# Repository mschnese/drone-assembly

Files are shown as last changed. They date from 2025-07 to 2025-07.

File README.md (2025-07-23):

# drone-assembly

## Objective: Build a drone from start to finish. I wanted to treat this like a rigorous personal project. I established a timeline, a budget, optimized my BOM, 3d modeled and printed my drone's frame, analyzed the frame through FEA and tests in real life, made every decision based on a justification, documented every step, and created a writeup for it.

## Contents: Assorted media from each stage of the project and the technical report

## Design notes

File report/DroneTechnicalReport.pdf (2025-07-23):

Matthew Schnese | 1

# Independent Drone Project

Building a Drone Utilizing CAD, FEA, Iterative Prototyping, and Betaflight Tuning.

## Matthew Schnese

6/23/2025

## Abstract:

The goal of this project was to build a functional quad copter drone capable of stable flight leveraging an engineering skillset, all while treating the project as a rigorous engineering endeavor. This included a bill of materials, a timeline, designing the drone’s frame, and justification for each action taken. Overall, the project encountered hurdles from every step. Some were entirely user errors, like poor solders, and others were inevitable, such as software issues. Some errors, however, were due to inexperience in engineering projects, such as GD&T or weight and size considerations. These errors were extremely valuable to learn from firsthand. The result of the project was a successful controlled flight; however, a critical failure of an ESC has grounded the project for the time being. While this is unfortunate, this is not a stopping point for this project but rather a simple part replacement.

## Table of Contents:

### 1. Introduction: pg. 4

### 2. Methodology: pg. 5

### 3. Analysis and Results: pgs. 6-8

### 4. Challenges and Conclusion: pg. 9

### 5. References: pg. 10

### 6. Appendices: pg. 11-14

## Introduction:

This report documents the design and construction of a drone, which was built as a

personal project during the summer break in between semesters. The motivations of this project

were to tackle an engineering project without guidance and to satisfy personal curiosity. This

project was meant not to be an informal side project, but rather a strict, well documented, and

rigorous project that would better mimic real life. A scope was established with the conception of

this project, and every design decision was documented thoroughly. Along with this, there was

also a tangible goal for success for each step of the drone assembly.

The scope of this project, from the start, has been well defined; the final drone design was

intended to be handheld, and flown via line of sight. Additionally, the weight of the drone was

monitored to comply with FAA regulation. Drones that weigh more than 250g must be registered

with the FAA [1], so keeping the drone under 250g was essential. For the design of the drone, I

decided to model the drone’s frame using SolidWorks, but elected not to build the flight

controller manually to avoid scope creep. Additionally, a timeline was decided after initial

research as part of the scope, which was a total of 6 weeks from start to finish. The timeline for

this project was as follows: week 1 was research, week 2 was computer assisted design (CAD)

modeling, week 3 was frame testing and software familiarization, week 4 was assembly, week 5

was flight testing, and week 6 was reserved for delays and final touches. This was primarily to

avoid the feeling of a side project, but rather to make this an active project that required near

constant work, which better mimics an actual engineering project.

## Methodology:

At the beginning of this project, the parts were researched and chosen based on the clear

scope that had been developed. These parts were then compiled into a complete Bill of Materials,

which can be seen in appendix D. For this design project, a 4000kv brushless motor and the

propellers built for it were chosen due to the motor’s relatively low power, matching the scope of

the handheld drone. A 3S 850mAh LiPo battery was also chosen to complement the motor. The

selected flight controller was the Speedy Bee 405AIO, which has many DIY friendly features

like integrated electronic speed controllers (ESCs), BetaFlight software support, and a compact

size that serves well for smaller builds. Over the course of the project 3 prototypes were created.

The frame of the drone was a completely original work created with a combination of

CAD and additive manufacturing, specifically 3D printing. The drone’s frame was split into three

parts, the main body, the body’s lid, and modular arms. The main body was designed in a basket

shape with a size of 70mm×70mm×25mm, but later iterations increased the size to 85×85×30,

which let components fit better. The arms are 50mm long overall, featuring a hollowed-out well

for the motors to be mounted and 2 screws to mount the arm to the main body. This decision

allows for broken arms to be isolated and requires only a single arm to be made, not the entire

frame. The entire design was optimized for easy assembly, requiring 12 m3x8mm screws, with 4

for the lid and 2 for each arm.

For the 3D printing of the frame, specific choices were made to maximize the strength of

the drone’s frame while minimizing weight. All three parts of the frame were printed using

PLA+, which was chosen due to material availability at the time. Additionally, the frame was

printed with a 30% infill, which means the printed part has 30% of the normal density of the

printing material, and a gyroid pattern which is a great choice for strength in all directions.

Supports were used, but only on overhangs that were over the build plate. This design decision

stopped supports from printing in hard-to-reach places, which was easier for assembly but

slightly reduced strength because of inefficient first layer bonding on some overhangs. Some

other minor print settings included a nozzle temperature of 215° C and a build plate temperature

of 65° C. Once the frame was printed, the edges were sanded, and the supports were removed.

## Analysis and Results:

The drone frame was analyzed using both finite element analysis (FEA) and real-life

testing. While FEA testing was only performed for the final design, each prototype was tested in

real life. The tests performed were a drop test at various heights, a load test for both the frame

and the arm, and weighing the drone to ensure flight was possible. The drop tests were conducted

on concrete, starting at one foot and increasing in increments of one foot each time until a height

of six feet. While the drone was not dropped with a simulated load weight, it is believed that the

rough concrete mitigated this potential source of error in testing. The load tests performed for the

main body and the arm were a load of 200lb and a load of 2lb respectively. These tests can be

seen in appendix A. The weight of the frame did not have a strict value in mind, but for flight to

be possible (and responsive), a weight of 50-100g was required for the full frame.

The first prototype passed all the load tests but could not be assembled because the

intended screw holes were not wide enough and screws were stripped during assembly. The first

prototype also failed the weight requirement with a weight of 46g, just under the lower limit. The

second prototype was able to be assembled, increased in size for better part accommodation, and

passed every test except the drop test, which had an arm break on the 6ft drop due to a force

concentration, all while weighing 96g. The third prototype increased the strength of the arm and

the connection while shaving weight and resulted in the same experimental outcome as the

second prototype while weighing 88g. It is worth noting that the severity of the break, while the

same in nature, decreased in severity from the second and third prototype. While these breaks do

showcase a failure point, breaking at the arm connection is preferred due to the modular nature

of the arm, and therefore is not a failure structurally. Since the electronics inside the main frame

are worth far more than the motor and arm, even if the motor is permanently damaged that is a

better outcome than the overall body receiving a large impact and breaking. Images of these

breaks can be seen below in Figure 1a and 1b.

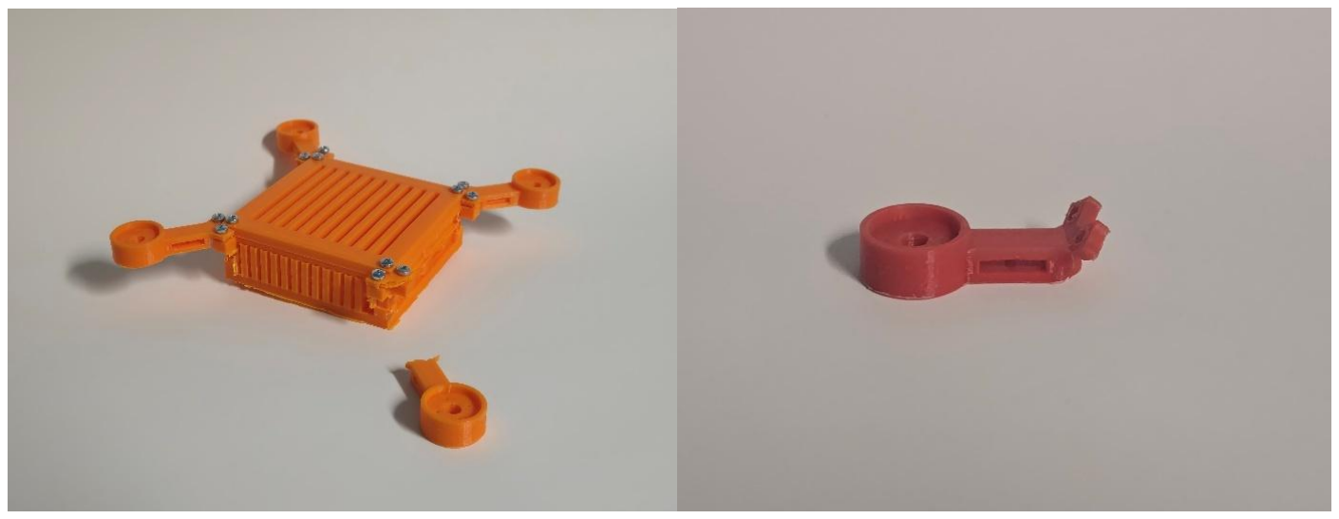
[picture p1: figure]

Figure 1: Drop Test Breaks – (a) Prototype 2, (b) Prototype 3

For the final design, FEA testing was implemented with five studies overall: two on the

arm and three on the body. For the arm, studies were run for lift forces and torque from the

motor, with the failure load and torque found to be 7.885 lbf and 15.76 lbf ·in respectively.

According to the manufacturer, the chosen motor’s maximum thrust on a 4S LiPo battery per

motor is 290g [2]. For a 3S battery setup like the one in this project, a maximum lift of about 200

g or 0.44 lbf is more practical, which is way below the failure point of the arm. The torque

generated by the motor was calculated using Equation 1, which can be seen below.

T = tℎrust × rpropeller

Since the propeller for this project has a 2.5-inch diameter, the total torque produced by

one motor is 0.55lbf ·in, which is well below the yield strength of the arm as well. While the arm

performed very well on the FEA analysis, it is worth pointing out that the failure point in FEA

also correlates with real life very well. This can be seen below in Figure 2.

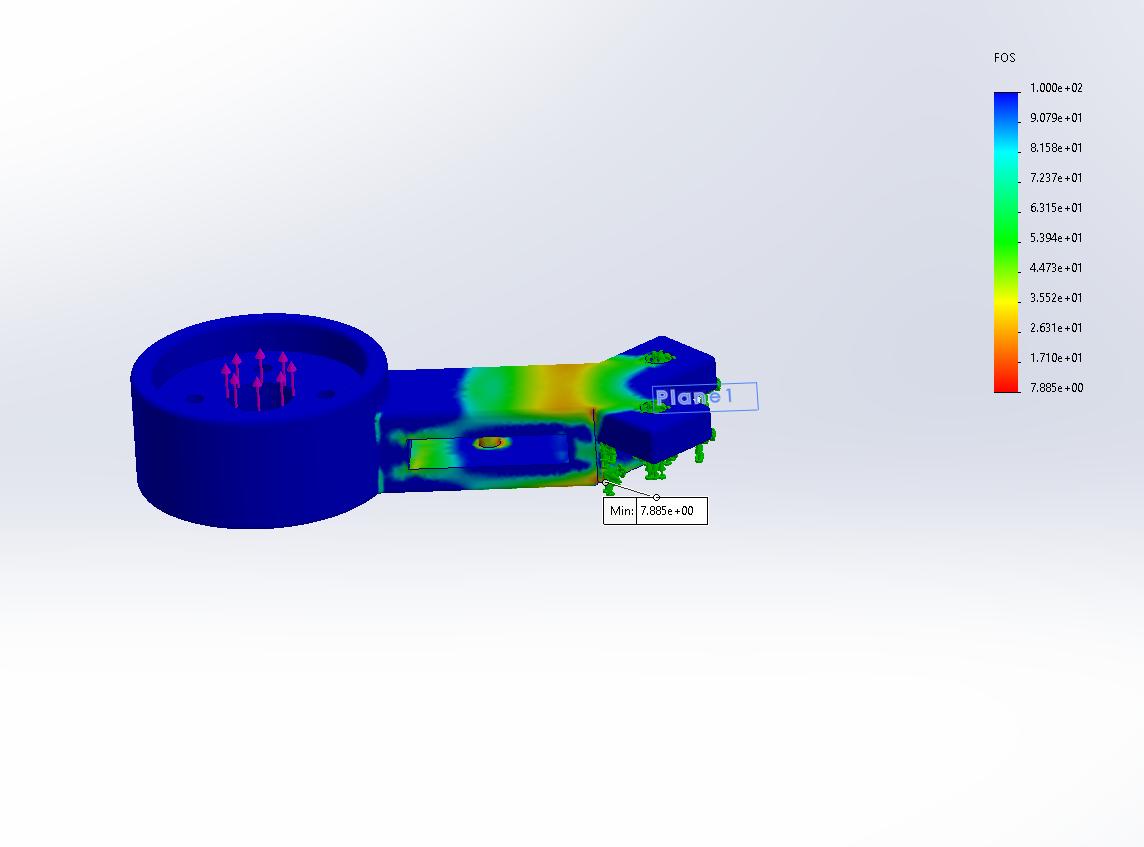
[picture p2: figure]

Figure 2: FEA Analysis Failure Points for Lift

For the body, similar studies were run concerning lift and torque on the connection where

the arm attaches, and a study was run on the load that the base of the drone frame could

withstand. For the lift and torque studies, the main connection point had a failure load and torque

of 122.3 lbf and 8.895 lbf·in respectively. For the load study, the analysis showed a maximum

load of 111.6 lbf. This particular result was interesting since real load testing showed that the

frame survived loads of 200 lbf. Because of this discrepancy, further load testing was conducted,

and it was found that the drone body could withstand over 285 lbf of load without breaking. This

highlights the differences between FEA analysis and real testing.

## Challenges and Conclusion:

During this project, there were many engineering challenges that had to be overcome.

From frame design to thermal issues on the flight controller, every step had a major issue that

needed to be addressed. During the initial frame design, many issues were discovered after

manufacturing the frame. From the size of the frame to the size of the screw holes to the design

of the arms, each piece was fine in theory but turned out to not work practically due to things like

GD&T. Soldering was also a major hurdle, since I have little soldering experience. The wiring

diagram for this project can be seen in appendix B. The connection wires for the battery and the

wires to the motors were a large gauge, which was a challenge to solder properly with the small

flight controller pads. Additionally, since this system underwent crashes during flight tests and

the wires were bent to accommodate space, often solders became undone and the whole

assembly had to be taken apart. During the soldering process, an ESC was fried internally on the

flight controller due to an undiscovered short, which has ceased flight.

When there wasn’t a mechanical issue, there was a software issue. Building a drone has

some complexities that are hidden inside the software used, which was Betaflight, like

determining the spin of the motors, or correctly accounting for the offset of the flight controller.

Some other examples of technical difficulties I faced during this project were the motors creating

lift upon arming even without throttle, connecting the transmitter to the receiver, or determining

the cause of RX loss. A more comprehensive list of errors and the solutions I found can be found

in appendix C.

Despite the many hurdles I faced, this project has given me very valuable experience on

every part of an engineering project. From choosing parts to optimizing the frame to mechanical

and software error handling, I encountered just about every error I could and learned how to

effectively solve problems and build intuition. Despite these many errors, the project’s goal of

building a stable drone capable of flight was accomplished, which can be seen in the media

section of the project’s GitHub. For future work on this project, the next step would be to replace

the flight controller due to the fried ESC, and future upgrades could include a First Person View

(FPV) camera and a 4S LiPo battery.

## References:

[1] FAA – Recreational Drone Registration Guidelines

https://www.faa.gov/uas/getting_started/register_drone

[2] BETAFPV - Lava Series 1506 Brushless Motors

https://betafpv.com/collections/brushless-motors/products/lava-series-1506-

brushless-motors (https://betafpv.com/collections/brushless-motors/products/lava-series-1506-brushless-motors)

## Appendix A: Load Testing

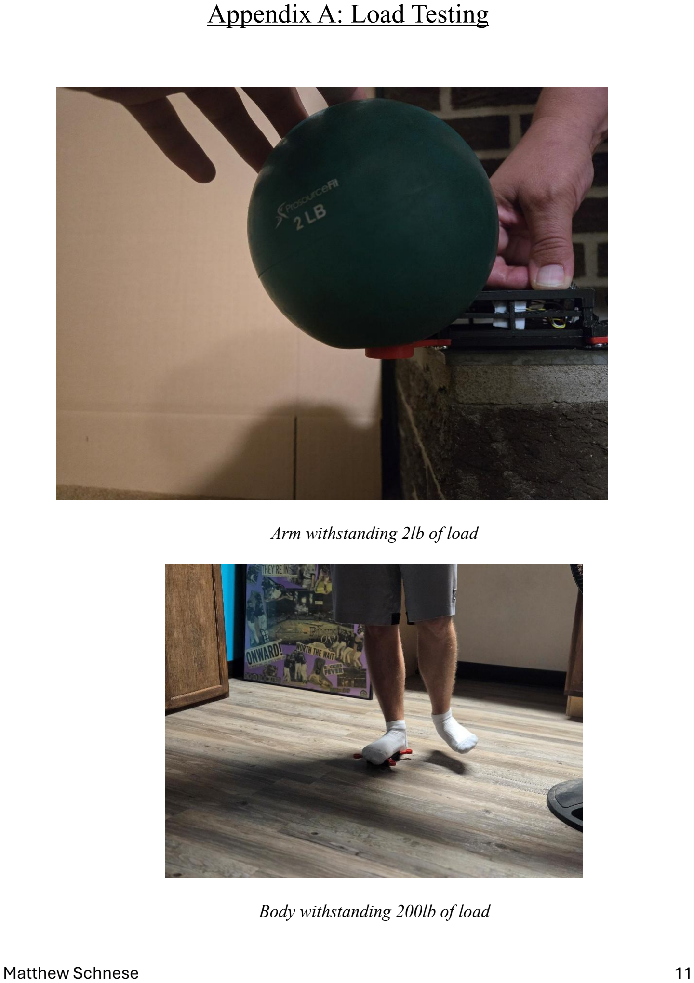
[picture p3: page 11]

Arm withstanding 2lb of load

Body withstanding 200lb of load

## Appendix B: Wiring Diagram

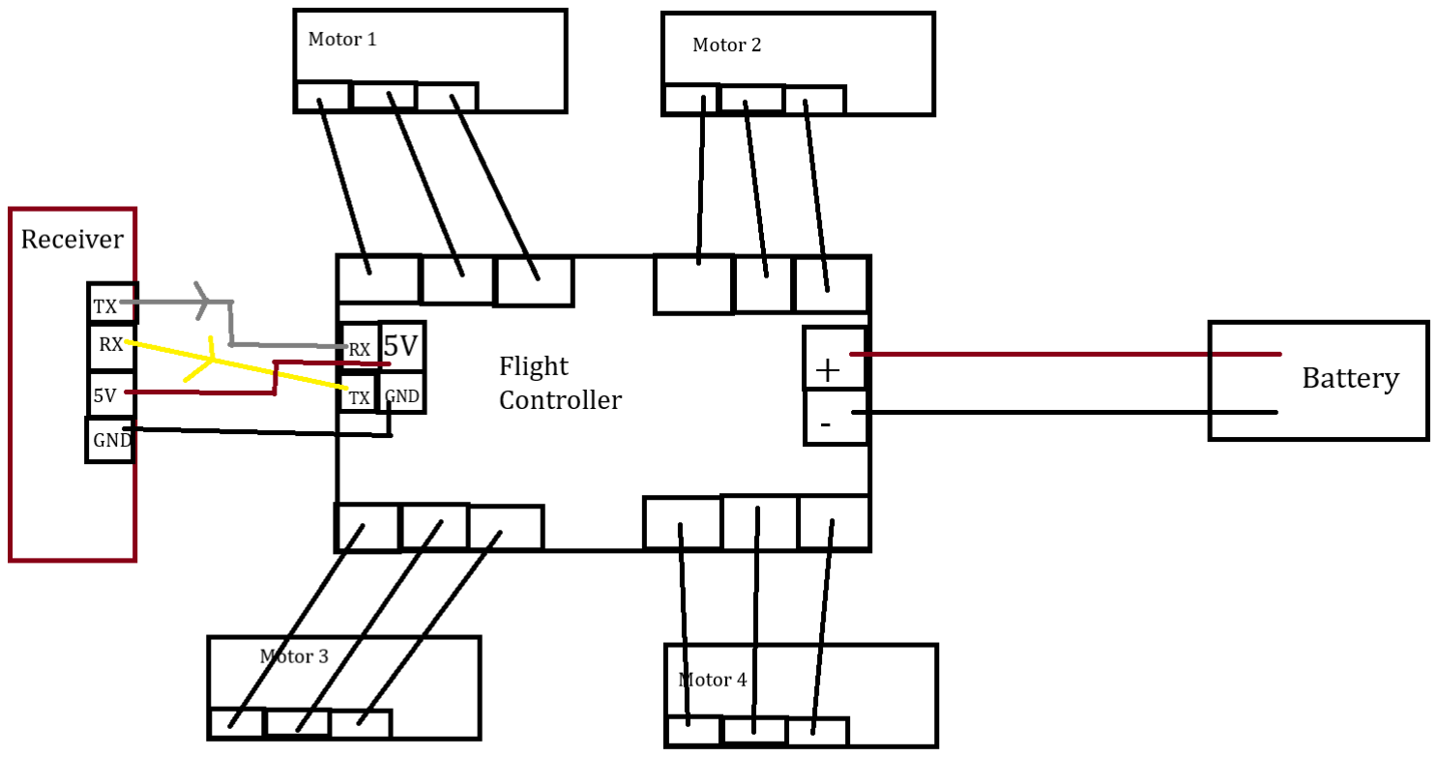
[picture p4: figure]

Wiring Diagram for the Flight Controller Made in MS Paint

## Appendix C: Error and Solution Table

Error: | Solution:
Drone Frame was Too Small | Dimensions increased from 70x70x25mm to 85x85x30mm
Screw holes were too small | Screw holes increased from 2.5 to 2.6mm
Frame too heavy | Support pillars decreased in size; air vents increased in size and quantity
Arms were stress concentration points | Not addressed; arms designed to break before frame
Drone produced lift even with no throttle | PID tuning turned off before certain % throttle, dshot_idle_value decreased
UART 3 port fried during soldering causing RX Loss in CLI | Switched to UART 5
No room for battery in drone frame | Battery wrapped in foam and electrical tape, strapped to bottom.
Flight controller overheating | Unable to be addressed; caused by soldering mistake and fried internal component
Drone drifts in flight testing | Center of mass shifted until drift was manageable
Motor wires are too short to solder | Flight controller mounted at 45-degree angle for ease of access
Final Drone Prototype was 4 grams over 250g weight limit | Air vents on non-load bearing regions expanded to reduce material

## Appendix D: Bill of Materials

Item | Cost | Link
Soldering Iron Kit | 17.99 | https://a.co/d/6YskGMB
Test Kit | 18.99 | https://a.co/d/98i73YK
Solder | 11.99 | https://a.co/d/1helH4b
Flight Controller | 59.99 | https://a.co/d/hUkwHap
Transmitter | 52.99 | https://a.co/d/3yBquBF
Receiver | 23.99 | https://a.co/d/6LJXERT
Motors | 14.99×4 | https://betafpv.com/collections/brushless-motors/products/lava-series-1506-brushless-motors (https://betafpv.com/collections/brushless-motors/products/lava-series-1506-brushless-motors)
Propellers | 2.50×3 | https://betafpv.com/products/gemfan-d63-3-blade-propellers-1-5mm-shaft?_pos=1&_sid=51054b8a4&_ss=r (https://betafpv.com/products/gemfan-d63-3-blade-propellers-1-5mm-shaft?_pos=1&_sid=51054b8a4&_ss=r)
3S LiPo Batteries | 29.99 | https://a.co/d/i0Bczd0
Battery Charger | 9.68 | https://a.co/d/9skja1B
Velcro Straps | 8.99 | https://a.co/d/4vgneQ5
XT30 Battery Connectors | 9.99 | https://a.co/d/9tj3u2S
Total | 312.05

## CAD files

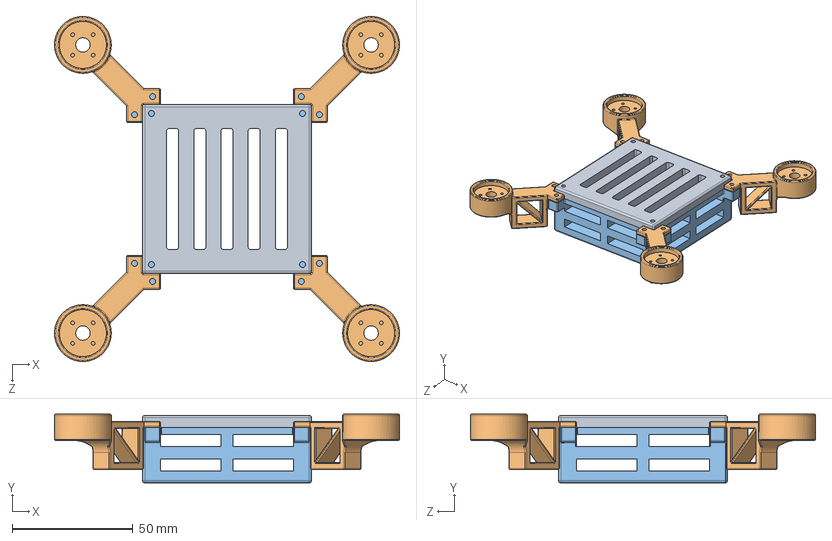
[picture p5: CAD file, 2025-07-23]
solidworks/Assembly.SLDASM
142.8 x 28.5 x 142.8 mm
Drone_Body_Lower
Drone_Arm x 4
Drone_Body_Upper

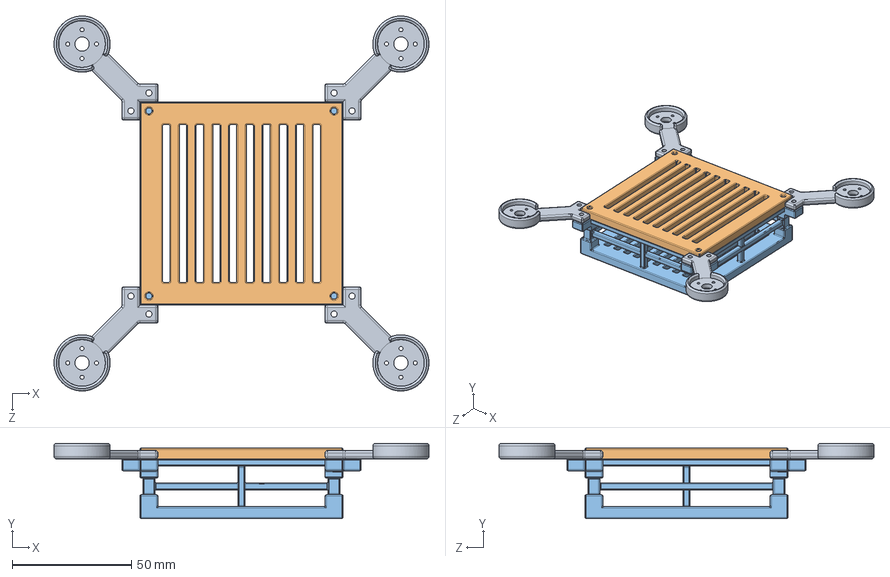
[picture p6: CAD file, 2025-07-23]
solidworks/AssemMK3.SLDASM
156.9 x 31.5 x 156.9 mm
Drone_body_lower_MK3
Drone_body_upper_MK3
Drone_Arm_MK3 x 4

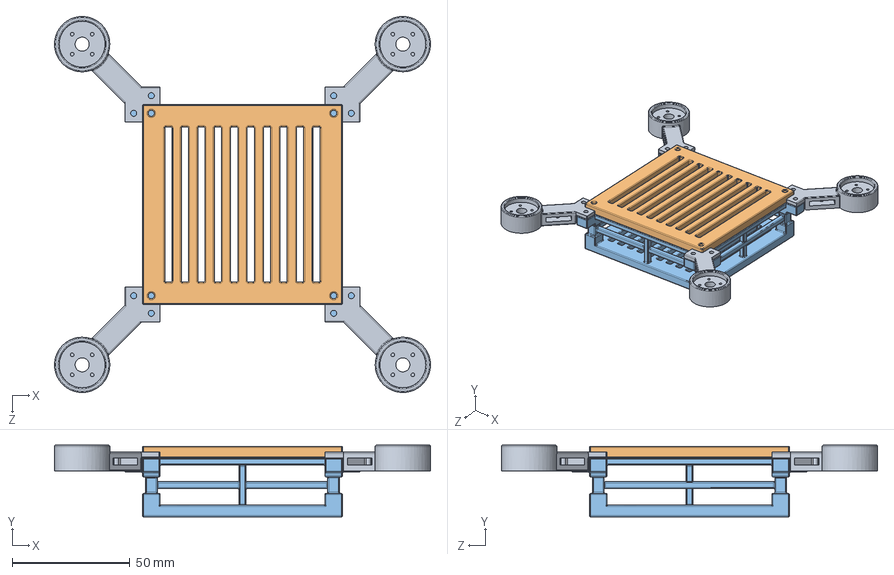
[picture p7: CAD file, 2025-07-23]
solidworks/AssemMK2.SLDASM
159.8 x 30.5 x 159.8 mm
Drone_body_lower_MK2
Drone_body_upper_MK2
Drone_Arm_MK2 x 4

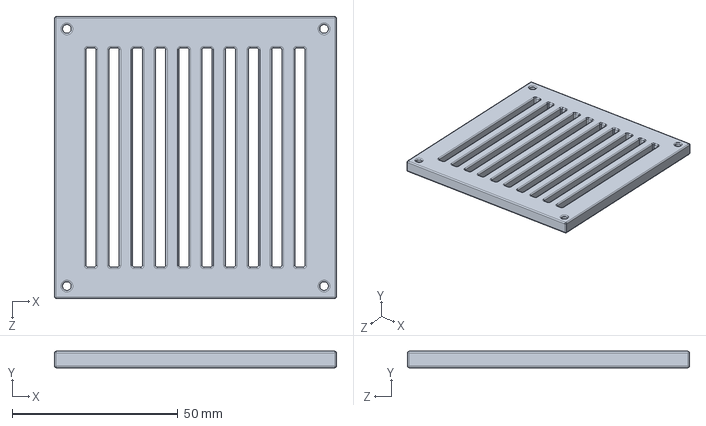
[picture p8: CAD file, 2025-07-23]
solidworks/Drone_body_upper_MK3.SLDPRT
85.0 x 5.00 x 85.0 mm

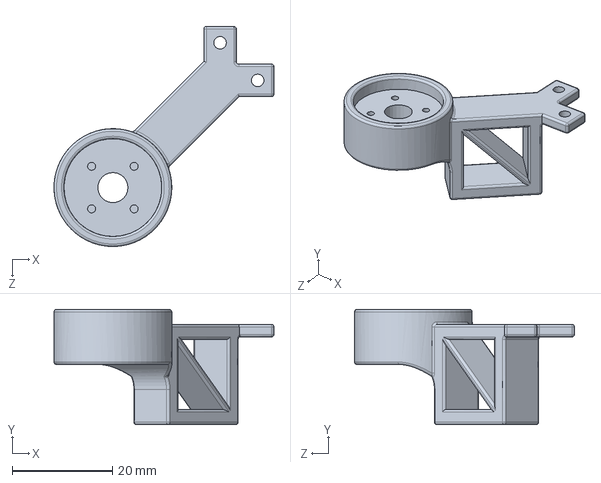
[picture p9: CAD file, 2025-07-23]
solidworks/Drone_Arm.SLDPRT
43.9 x 23.0 x 43.9 mm

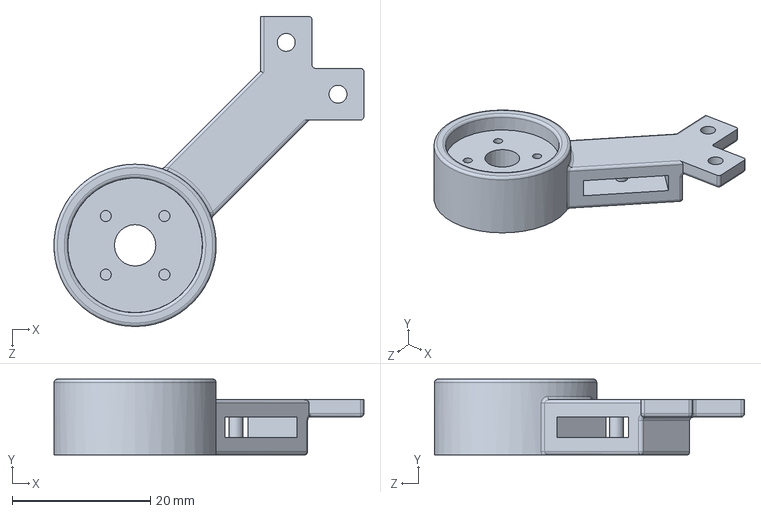
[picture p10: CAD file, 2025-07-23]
solidworks/Drone_Arm_MK2.SLDPRT
44.9 x 11.0 x 44.9 mm

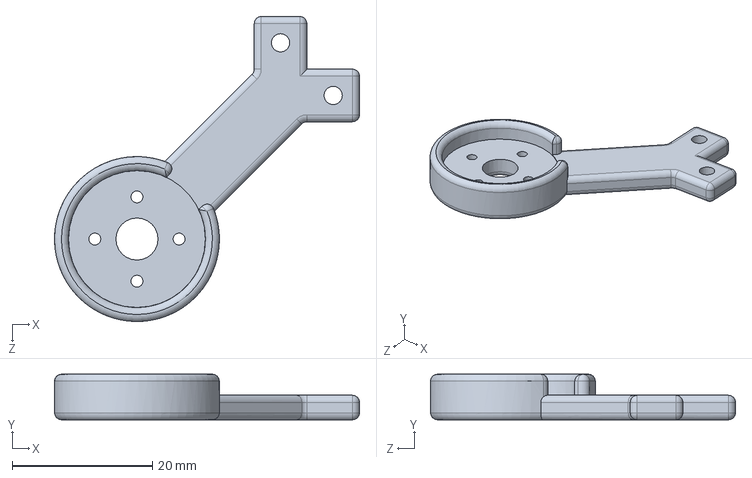
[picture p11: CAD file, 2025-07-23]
solidworks/Drone_Arm_MK3.SLDPRT
43.5 x 6.50 x 43.5 mm

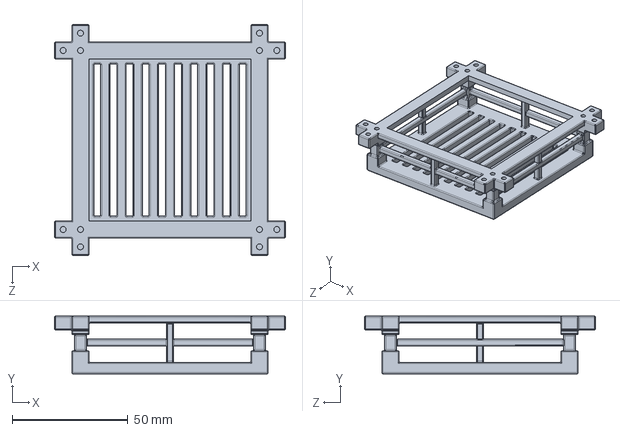
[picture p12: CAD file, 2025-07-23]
solidworks/Drone_body_lower_MK2.SLDPRT
100.0 x 25.0 x 100.0 mm

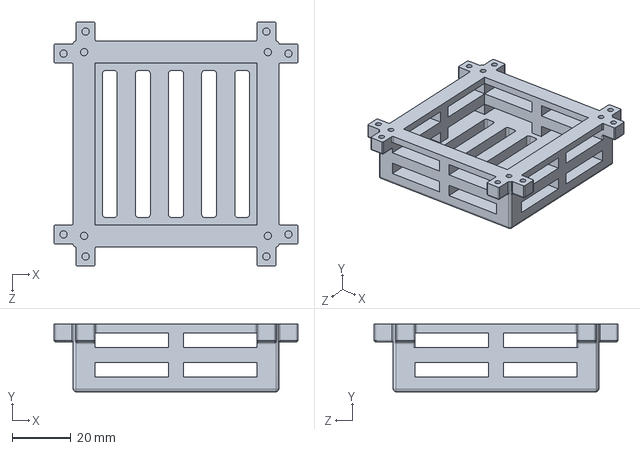
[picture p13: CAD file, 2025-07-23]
solidworks/Drone_Body_Lower.SLDPRT
83.0 x 23.0 x 83.0 mm

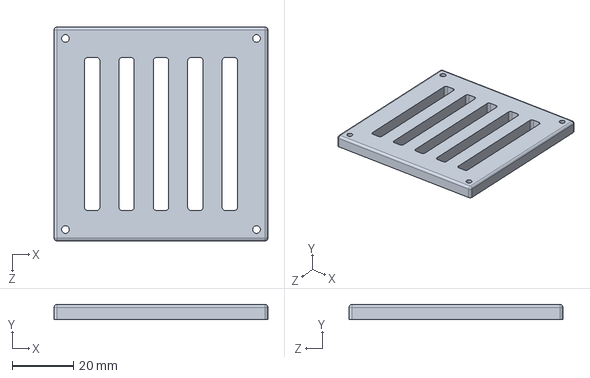
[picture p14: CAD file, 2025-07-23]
solidworks/Drone_Body_Upper.SLDPRT
70.0 x 5.00 x 70.0 mm

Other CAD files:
solidworks/Drone_body_upper_MK2.SLDPRT
solidworks/Drone_body_lower_MK3.SLDPRT
